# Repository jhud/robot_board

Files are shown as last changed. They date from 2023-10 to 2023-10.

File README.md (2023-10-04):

# Robot controller board

Controller board for building servo-based robots, such as hexapods.

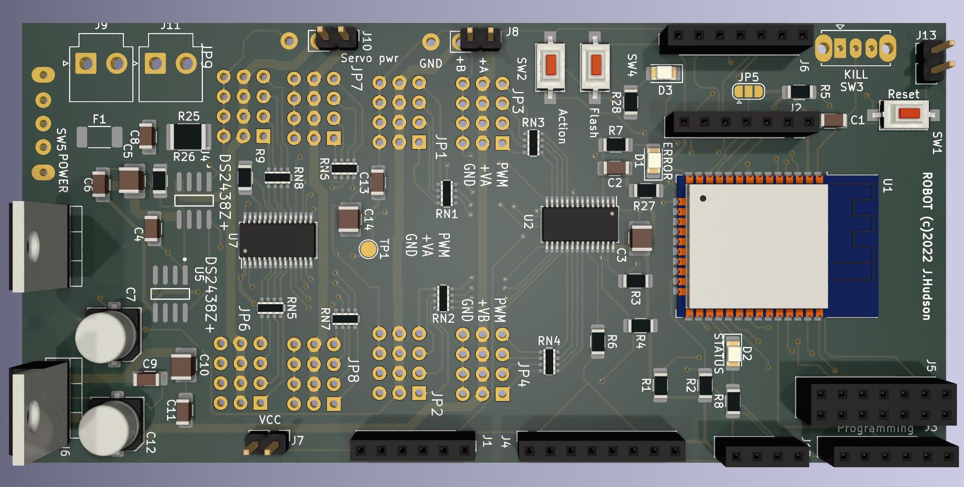
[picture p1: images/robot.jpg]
robot image

Render of board rev 2

This project was designed to allow rapid prototyping of different types of servos and sensors for walking robots: it's easy to switch out different sensors, and I2C buses are exposed for adding standard plugin components, such as those from Adafruit. But the board could be used for any projects needing a lot of servos.

The main benefit of this over a standard Arduino is the number of PWM pins and the server sockets, plus the power supply monitoring circuitry.

You should be able to get a standard "spiderbot" Arduino sketch running on this hardware quite easily: I'll shortly publish some test sketches and controller firmware.

Have fun!

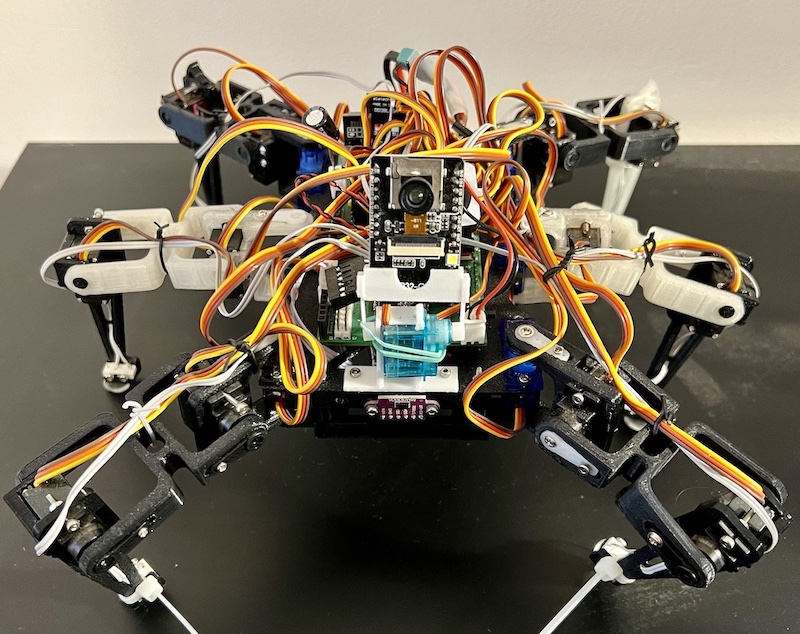
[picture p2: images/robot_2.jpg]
robot board

Board in action

## Features

Core features:
- ESP32 processor, Arduino compatible
- 32 PWM servo channels (ie max 10 legs)
- 6 foot contact sensors
- 7.6v LiPo battery, or power supply input
- Power supply monitoring for:
   - main battery voltage + current
   - 3.3v regulated rail voltage
   - 2x 5v rail servo voltages

With standard plugin modules installed in sockets:
- speech and audio output
- infrared beacon detection
- inertial measurement unit
- extra PWM channels

See it running here (video):

Hanging out with my robot and asking it to do things
[http://www.youtube.com/watch?v=hFirgdrsIpw](https://www.youtube.com/watch?v=hFirgdrsIpw)

## Building it

### ESP32 CAM

The ESP32 CAM module can run on 3.3v or 5v. If you are getting freezes and dropped frames from the camera, try running it from the robot's 5v rail instead of 3.3v.

The ESP32 CAM has a XC6206-2.8V regulator after its 3.3v regulator, and this component has a dropout voltage up to ~500mV according to the specs. My hypothesis is that the camera crashes on slight undervoltages.

So the 3.3v rail must be rock solid - this may not be the case with your regulator, so it's generally recommended to run the ESP32 CAM off the 5v rail. Even with many noisy servos, the camera works fine on the robot on the 5v rail.

### Pullup resistors

Pullups can vary between 2K and 10K - if there are problems communicating with I2C, try reducing the pullups. Higher pull-ups waste less power.

## Revisions

Note that the main branch is a work in progress: please take an earlier revision if you want a working layout. These are tested and working (with some minor noise issues and a couple of bodge wires needed).

- main branch is a work in progress: I am upgrading to ESP32-S3 and have fixed some noise issues and minor annoyances. Use an older tag if you want something that works.
- 2nd revision: 32 PWM channels onboard, 6 foot switches + power pins for IR proximity sensors
- 1st revision: 16 PWM channels, 4 foot switches

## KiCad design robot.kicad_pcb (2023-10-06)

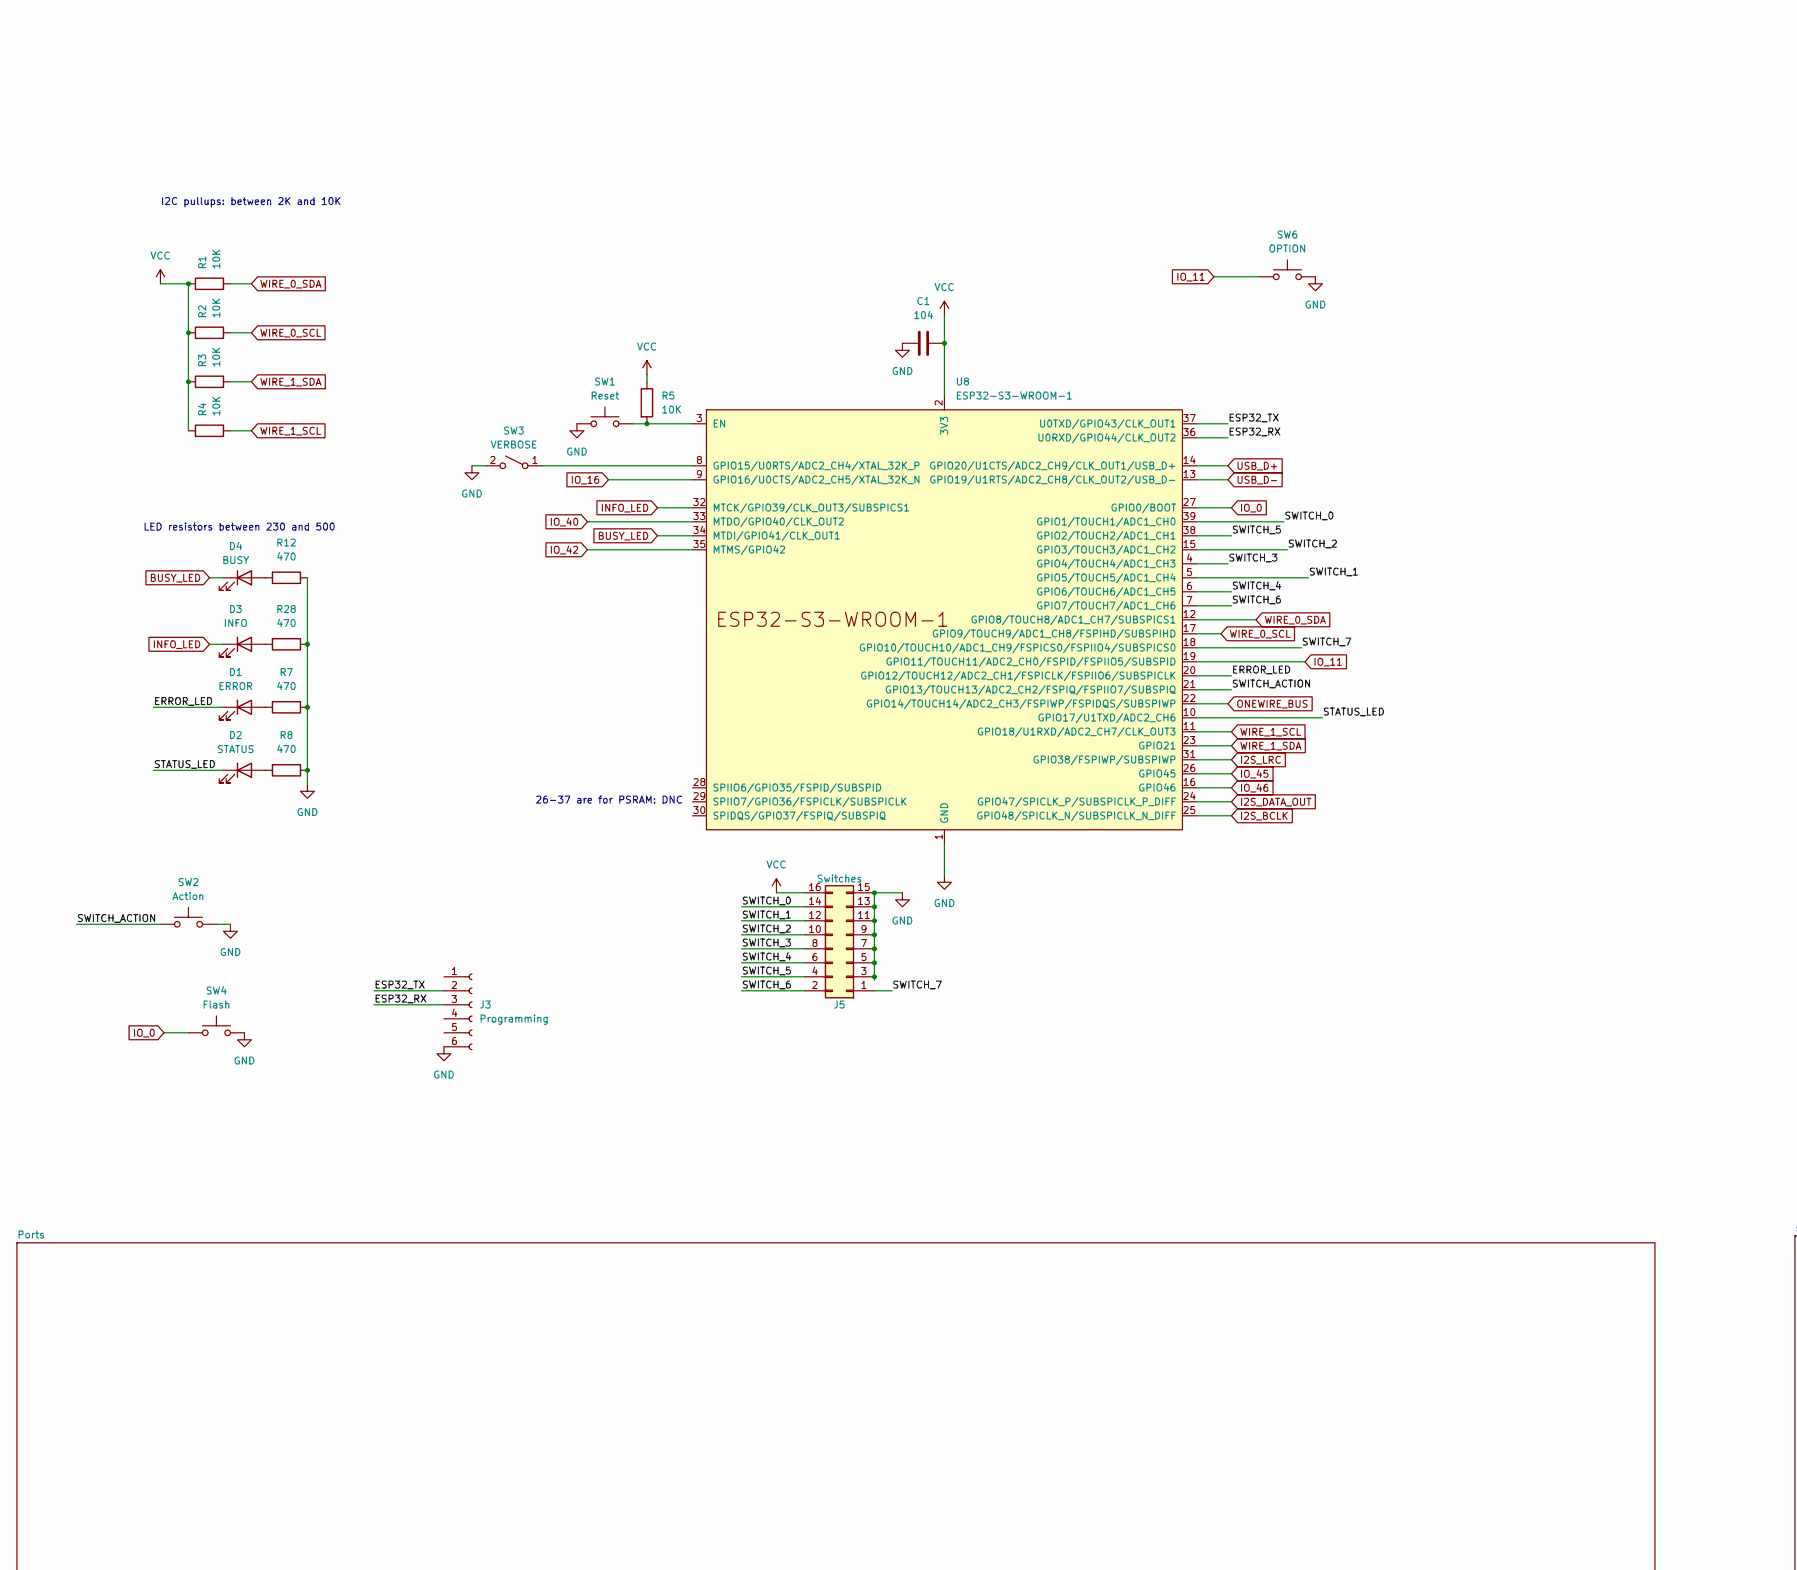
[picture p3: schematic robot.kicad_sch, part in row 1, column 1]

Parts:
C1: 104; C_1206_3216Metric_Pad1.33x1.80mm_HandSolder
D1: ERROR; LED_1206_3216Metric_Pad1.42x1.75mm_HandSolder
D2: STATUS; LED_1206_3216Metric_Pad1.42x1.75mm_HandSolder
D3: INFO; LED_1206_3216Metric_Pad1.42x1.75mm_HandSolder
D4: BUSY; LED_1206_3216Metric_Pad1.42x1.75mm_HandSolder
J3: Programming; PinSocket_1x06_P2.54mm_Vertical
J5: Switches; PinSocket_2x08_P2.54mm_Vertical
R1, R2, R3, R4, R5: 10K; R_1206_3216Metric_Pad1.30x1.75mm_HandSolder
R7, R8, R12, R28: 470; R_1206_3216Metric_Pad1.30x1.75mm_HandSolder
SW1: Reset; SW_SPST_CK_RS282G05A3
SW2: Action; SW_SPST_CK_RS282G05A3
SW3: VERBOSE; SW_Slide_1P2T_CK_OS102011MS2Q
SW4: Flash; SW_SPST_CK_RS282G05A3
SW6: OPTION; SW_SPST_CK_RS282G05A3
U8: ESP32-S3-WROOM-1; ESP32-S3-WROOM-1U

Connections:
/ERROR_LED: D1.1 (K), U8.20 (GPIO12/TOUCH12/ADC2_CH1/FSPICLK/FSPIIO6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)
/ESP32_RX: J3.3, U8.36 (U0RXD/GPIO44/CLK_OUT2)
/ESP32_TX: J3.2, U8.37 (U0TXD/GPIO43/CLK_OUT1)
/STATUS_LED: D2.1 (K), U8.10 (GPIO17/U1TXD/ADC2_CH6)
/SWITCH_0: J5.14, U8.39 (GPIO1/TOUCH1/ADC1_CH0)
/SWITCH_1: J5.12, U8.5 (GPIO5/TOUCH5/ADC1_CH4)
/SWITCH_2: J5.10, U8.15 (GPIO3/TOUCH3/ADC1_CH2)
/SWITCH_3: J5.8, U8.4 (GPIO4/TOUCH4/ADC1_CH3)
/SWITCH_4: J5.6, U8.6 (GPIO6/TOUCH6/ADC1_CH5)
/SWITCH_5: J5.4, U8.38 (GPIO2/TOUCH2/ADC1_CH1)
/SWITCH_6: J5.2, U8.7 (GPIO7/TOUCH7/ADC1_CH6)
/SWITCH_7: J5.1, U8.18 (GPIO10/TOUCH10/ADC1_CH9/FSPICS0/FSPIIO4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)
/SWITCH_ACTION: SW2.1, U8.21 (GPIO13/TOUCH13/ADC2_CH2/FSPIQ/FSPIIO7/S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)
BUSY_LED: D4.1 (K), U8.34 (MTDI/GPIO41/CLK_OUT1)
GND: C1.1, J3.6, J5.3, J5.5, J5.7, J5.9, J5.11, J5.13, J5.15, R7.1, R8.1, R12.1, R28.1, SW1.1, SW2.2, SW3.2 (B), SW4.2, SW6.2, U8.1 (GND), U8.40 (GND), U8.41 (GND); also elsewhere on the board
I2S_BCLK: U8.25 (GPIO48/SPICLK_N/SUBSPICLK_N_DIFF); also elsewhere on the board
I2S_DATA_OUT: U8.24 (GPIO47/SPICLK_P/SUBSPICLK_P_DIFF); also elsewhere on the board
I2S_LRC: U8.31 (GPIO38/FSPIWP/SUBSPIWP); also elsewhere on the board
INFO_LED: D3.1 (K), U8.32 (MTCK/GPIO39/CLK_OUT3/SUBSPICS1)
IO_0: SW4.1, U8.27 (GPIO0/BOOT)
IO_11: SW6.1, U8.19 (GPIO11/TOUCH11/ADC2_CH0/FSPID/FSPIIO5/S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)
IO_16: U8.9 (GPIO16/U0CTS/ADC2_CH5/XTAL_32K_N); also elsewhere on the board
IO_40: U8.33 (MTDO/GPIO40/CLK_OUT2); also elsewhere on the board
IO_42: U8.35 (MTMS/GPIO42); also elsewhere on the board
IO_45: U8.26 (GPIO45); also elsewhere on the board
IO_46: U8.16 (GPIO46); also elsewhere on the board
unnamed: D1.2 (A), R7.2
unnamed: D2.2 (A), R8.2
unnamed: D3.2 (A), R28.2
unnamed: D4.2 (A), R12.2
unnamed: SW3.1 (A), U8.8 (GPIO15/U0RTS/ADC2_CH4/XTAL_32K_P)
unnamed: R5.2, SW1.2, U8.3 (EN)
ONEWIRE_BUS: U8.22 (GPIO14/TOUCH14/ADC2_CH3/FSPIWP/FSPIDQS/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); also elsewhere on the board
USB_D+: U8.14 (GPIO20/U1CTS/ADC2_CH9/CLK_OUT1/USB_D+); also elsewhere on the board
USB_D-: U8.13 (GPIO19/U1RTS/ADC2_CH8/CLK_OUT2/USB_D-); also elsewhere on the board
VCC: C1.2, J5.16, R1.1, R2.1, R3.1, R4.1, R5.1, U8.2 (3V3); also elsewhere on the board
WIRE_0_SCL: R2.2, U8.17 (GPIO9/TOUCH9/ADC1_CH8/FSPIHD/SUBSPIHD); also elsewhere on the board
WIRE_0_SDA: R1.2, U8.12 (GPIO8/TOUCH8/ADC1_CH7/SUBSPICS1); also elsewhere on the board

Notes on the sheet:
26-37 are for PSRAM: DNC
LED resistors between 230 and 500
I2C pullups: between 2K and 10K

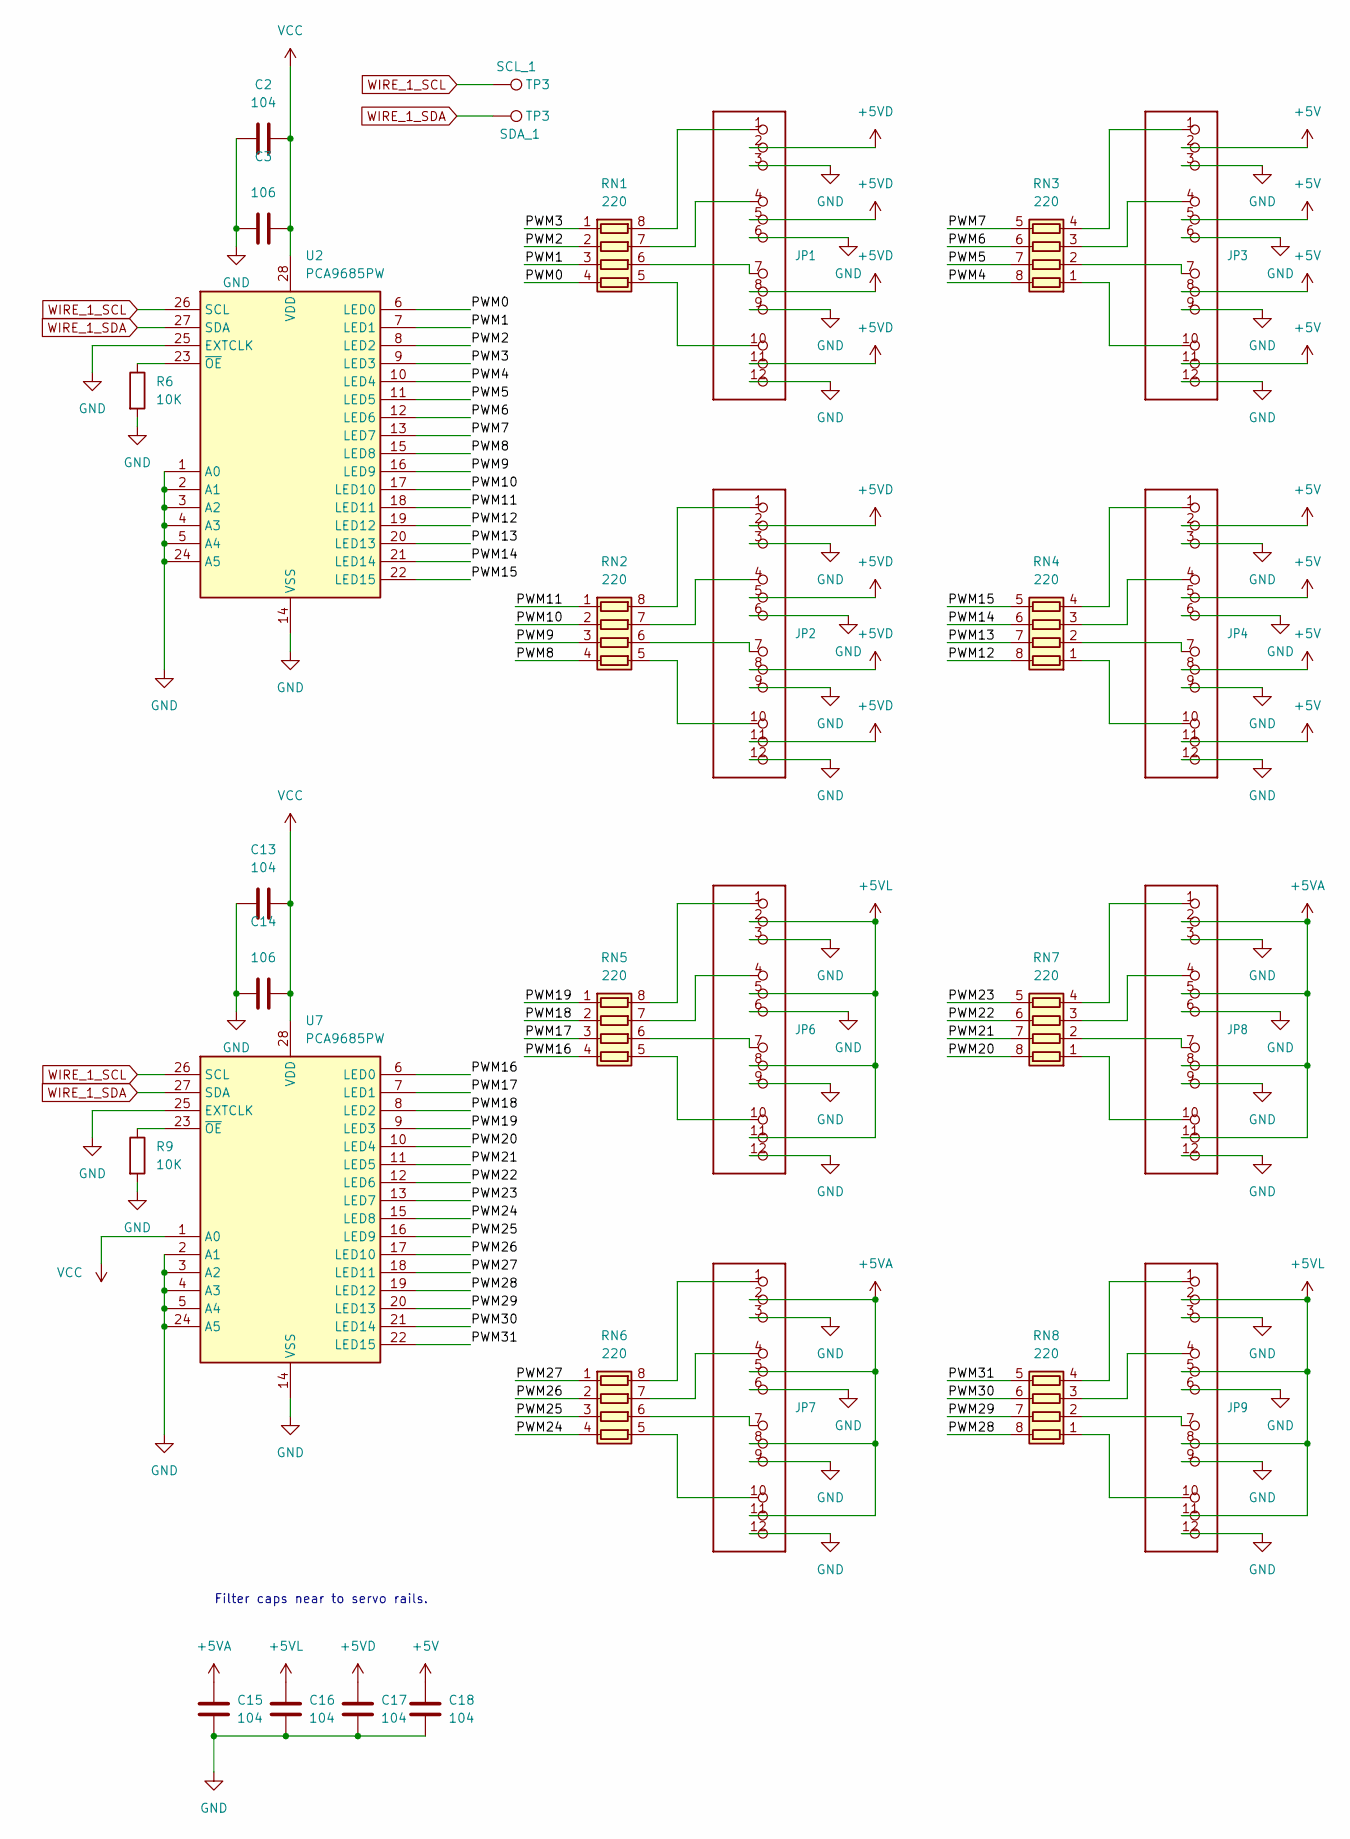
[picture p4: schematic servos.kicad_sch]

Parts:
C2, C13, C15, C16, C17, C18: 104; C_1206_3216Metric_Pad1.33x1.80mm_HandSolder
C3, C14: 106; C_1210_3225Metric_Pad1.33x2.70mm_HandSolder
JP1, JP2, JP3, JP4, JP6, JP7, JP8, JP9: HEADER-3X04; 3X04
R6, R9: 10K; R_1206_3216Metric_Pad1.30x1.75mm_HandSolder
RN1, RN2, RN3, RN4, RN5, RN6, RN7, RN8: 220; R_Array_Concave_4x0603
TP3: SCL_1; TestPoint_Pad_D2.0mm
U2, U7: PCA9685PW; TSSOP-28_4.4x9.7mm_P0.65mm

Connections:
+5V: C18.1, JP3.2, JP3.5, JP3.8, JP3.11, JP4.2, JP4.5, JP4.8, JP4.11; also elsewhere on the board
+5VD: C17.1, JP1.2, JP1.5, JP1.8, JP1.11, JP2.2, JP2.5, JP2.8, JP2.11; also elsewhere on the board
+5VL: C16.1, JP6.2, JP6.5, JP6.8, JP6.11, JP9.2, JP9.5, JP9.8, JP9.11; also elsewhere on the board
/servos/PWM0: RN1.4 (R4.1), U2.6 (LED0)
/servos/PWM1: RN1.3 (R3.1), U2.7 (LED1)
/servos/PWM2: RN1.2 (R2.1), U2.8 (LED2)
/servos/PWM3: RN1.1 (R1.1), U2.9 (LED3)
/servos/PWM4: RN3.8 (R1.2), U2.10 (LED4)
/servos/PWM5: RN3.7 (R2.2), U2.11 (LED5)
/servos/PWM6: RN3.6 (R3.2), U2.12 (LED6)
/servos/PWM7: RN3.5 (R4.2), U2.13 (LED7)
/servos/PWM8: RN2.4 (R4.1), U2.15 (LED8)
/servos/PWM9: RN2.3 (R3.1), U2.16 (LED9)
/servos/PWM10: RN2.2 (R2.1), U2.17 (LED10)
/servos/PWM11: RN2.1 (R1.1), U2.18 (LED11)
/servos/PWM12: RN4.8 (R1.2), U2.19 (LED12)
/servos/PWM13: RN4.7 (R2.2), U2.20 (LED13)
/servos/PWM14: RN4.6 (R3.2), U2.21 (LED14)
/servos/PWM15: RN4.5 (R4.2), U2.22 (LED15)
/servos/PWM16: RN5.4 (R4.1), U7.6 (LED0)
/servos/PWM17: RN5.3 (R3.1), U7.7 (LED1)
/servos/PWM18: RN5.2 (R2.1), U7.8 (LED2)
/servos/PWM19: RN5.1 (R1.1), U7.9 (LED3)
/servos/PWM20: RN7.8 (R1.2), U7.10 (LED4)
/servos/PWM21: RN7.7 (R2.2), U7.11 (LED5)
/servos/PWM22: RN7.6 (R3.2), U7.12 (LED6)
/servos/PWM23: RN7.5 (R4.2), U7.13 (LED7)
/servos/PWM24: RN6.4 (R4.1), U7.15 (LED8)
/servos/PWM25: RN6.3 (R3.1), U7.16 (LED9)
/servos/PWM26: RN6.2 (R2.1), U7.17 (LED10)
/servos/PWM27: RN6.1 (R1.1), U7.18 (LED11)
/servos/PWM28: RN8.8 (R1.2), U7.19 (LED12)
/servos/PWM29: RN8.7 (R2.2), U7.20 (LED13)
/servos/PWM30: RN8.6 (R3.2), U7.21 (LED14)
/servos/PWM31: RN8.5 (R4.2), U7.22 (LED15)
GND: C2.2, C3.1, C13.2, C14.1, C15.2, C16.2, C17.2, C18.2, JP1.3, JP1.6, JP1.9, JP1.12, JP2.3, JP2.6, JP2.9, JP2.12, JP3.3, JP3.6, JP3.9, JP3.12, JP4.3, JP4.6, JP4.9, JP4.12, JP6.3, JP6.6, JP6.9, JP6.12, JP7.3, JP7.6, JP7.9, JP7.12, JP8.3, JP8.6, JP8.9, JP8.12, JP9.3, JP9.6, JP9.9, JP9.12, R6.2, R9.2, U2.1 (A0), U2.2 (A1), U2.3 (A2), U2.4 (A3), U2.5 (A4), U2.14 (VSS), U2.24 (A5), U2.25 (EXTCLK), U7.2 (A1), U7.3 (A2), U7.4 (A3), U7.5 (A4), U7.14 (VSS), U7.24 (A5), U7.25 (EXTCLK); also elsewhere on the board
unnamed: JP1.1, RN1.8 (R1.2)
unnamed: JP1.4, RN1.7 (R2.2)
unnamed: JP1.7, RN1.6 (R3.2)
unnamed: JP1.10, RN1.5 (R4.2)
unnamed: JP2.1, RN2.8 (R1.2)
unnamed: JP2.4, RN2.7 (R2.2)
unnamed: JP2.7, RN2.6 (R3.2)
unnamed: JP2.10, RN2.5 (R4.2)
unnamed: JP3.10, RN3.1 (R1.1)
unnamed: JP3.7, RN3.2 (R2.1)
unnamed: JP3.4, RN3.3 (R3.1)
unnamed: JP3.1, RN3.4 (R4.1)
unnamed: JP4.10, RN4.1 (R1.1)
unnamed: JP4.7, RN4.2 (R2.1)
unnamed: JP4.4, RN4.3 (R3.1)
unnamed: JP4.1, RN4.4 (R4.1)
unnamed: JP6.1, RN5.8 (R1.2)
unnamed: JP6.4, RN5.7 (R2.2)
unnamed: JP6.7, RN5.6 (R3.2)
unnamed: JP6.10, RN5.5 (R4.2)
unnamed: JP7.1, RN6.8 (R1.2)
unnamed: JP7.4, RN6.7 (R2.2)
unnamed: JP7.7, RN6.6 (R3.2)
unnamed: JP7.10, RN6.5 (R4.2)
unnamed: JP8.10, RN7.1 (R1.1)
unnamed: JP8.7, RN7.2 (R2.1)
unnamed: JP8.4, RN7.3 (R3.1)
unnamed: JP8.1, RN7.4 (R4.1)
unnamed: JP9.10, RN8.1 (R1.1)
unnamed: JP9.7, RN8.2 (R2.1)
unnamed: JP9.4, RN8.3 (R3.1)
unnamed: JP9.1, RN8.4 (R4.1)
unnamed: R6.1, U2.23 (~OE)
unnamed: R9.1, U7.23 (~OE)
VCC: C2.1, C3.2, C13.1, C14.2, U2.28 (VDD), U7.1 (A0), U7.28 (VDD); also elsewhere on the board

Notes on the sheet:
Filter caps near to servo rails.

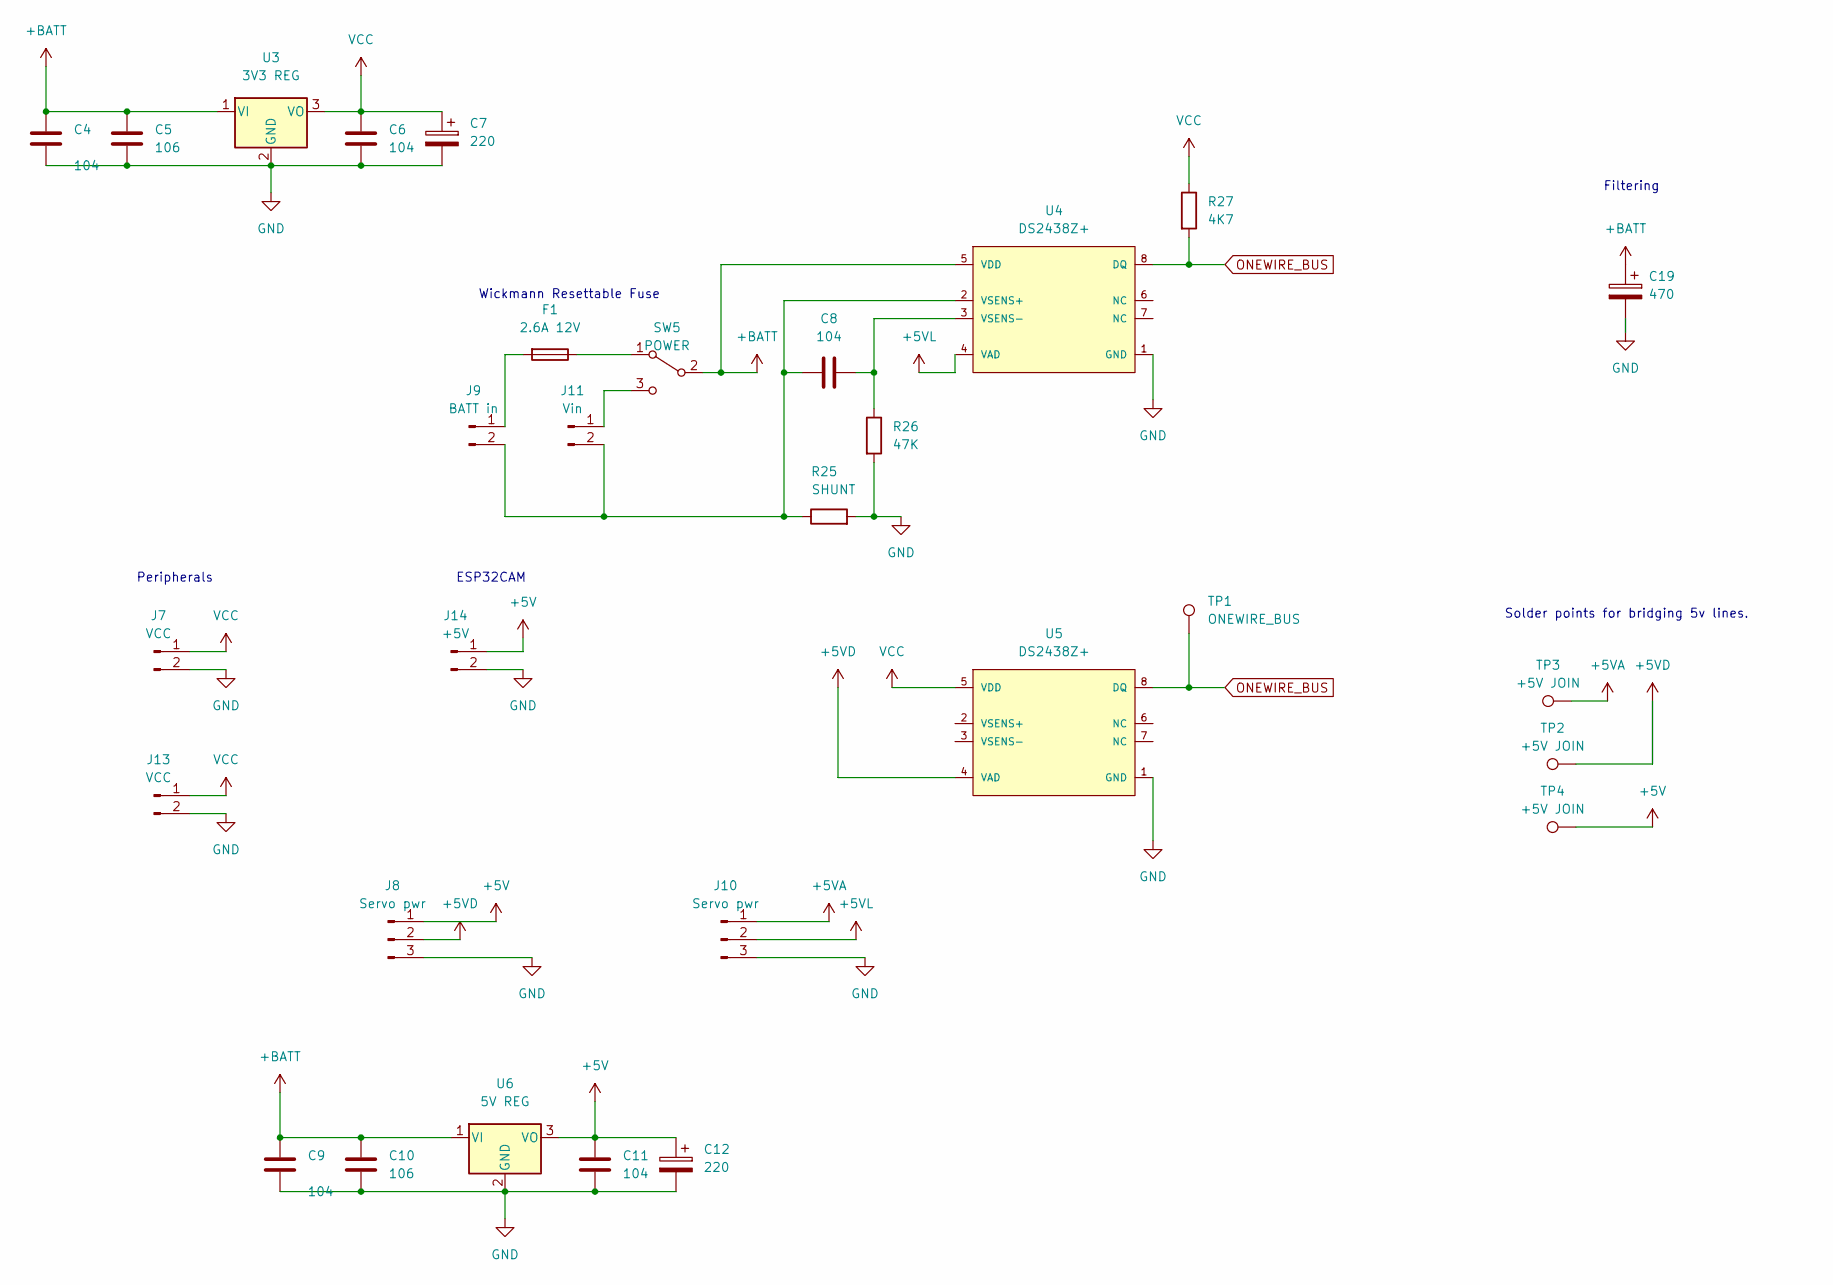
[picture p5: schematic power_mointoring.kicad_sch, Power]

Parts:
C4, C6, C8, C9, C11: 104; C_1206_3216Metric_Pad1.33x1.80mm_HandSolder
C5, C10: 106; C_1210_3225Metric_Pad1.33x2.70mm_HandSolder
C7, C12: 220; C_Elec_6.3x5.4
C19: 470; C_Elec_6.3x7.7
F1: 2.6A 12V; Fuse_2010_5025Metric
J7, J13: VCC; PinHeader_1x02_P2.54mm_Vertical
J8, J10: Servo pwr; Connector_SolderPadsx3
J9: BATT in; JST_VH_B2P-VH-B_1x02_P3.96mm_Vertical
J11: Vin; JST_VH_B2P-VH-B_1x02_P3.96mm_Vertical
J14: +5V; PinHeader_1x02_P2.54mm_Vertical
R25: SHUNT; R_1812_4532Metric_Pad1.30x3.40mm_HandSolder
R26: 47K; R_1206_3216Metric_Pad1.30x1.75mm_HandSolder
R27: 4K7; R_1206_3216Metric_Pad1.30x1.75mm_HandSolder
SW5: POWER; Switch-SS12F23
TP1: ONEWIRE_BUS; TestPoint_Pad_D2.0mm
TP2, TP3, TP4: +5V JOIN; TestPoint_Pad_D2.0mm
U3: 3V3 REG; TO-220-3_Vertical
U4, U5: DS2438Z+; Maxim-S8-5-0-P-IPC_A; mouser part number 700-DS2438Z; digikey description IC MONITOR SMART BATTERY 8-SOIC
U6: 5V REG; TO-220-3_Vertical

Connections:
+5V: C11.1, C12.1, J8.1, J14.1, TP4.1, U6.3 (VO); also elsewhere on the board
+5VD: J8.2, TP2.1, U5.4 (VAD); also elsewhere on the board
+5VL: J10.2, U4.4 (VAD); also elsewhere on the board
+BATT: C4.1, C5.1, C9.1, C10.1, C19.1, SW5.2 (B), U3.1 (VI), U4.5 (VDD), U6.1 (VI)
GND: C4.2, C5.2, C6.2, C7.2, C9.2, C10.2, C11.2, C12.2, C19.2, J7.2, J8.3, J10.3, J13.2, J14.2, R25.2, R26.2, U3.2 (GND), U4.1 (GND), U5.1 (GND), U6.2 (GND); also elsewhere on the board
unnamed: F1.2, J9.1
unnamed: J11.1, SW5.3 (C)
unnamed: C8.2, J9.2, J11.2, R25.1, U4.2 (VSENS+)
unnamed: F1.1, SW5.1 (A)
unnamed: C8.1, R26.1, U4.3 (VSENS-)
ONEWIRE_BUS: R27.2, TP1.1, U4.8 (DQ), U5.8 (DQ); also elsewhere on the board
VCC: C6.1, C7.1, J7.1, J13.1, R27.1, U3.3 (VO), U5.5 (VDD); also elsewhere on the board

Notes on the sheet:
Filtering
ESP32CAM
Solder points for bridging 5v lines.
Wickmann Resettable Fuse
Peripherals

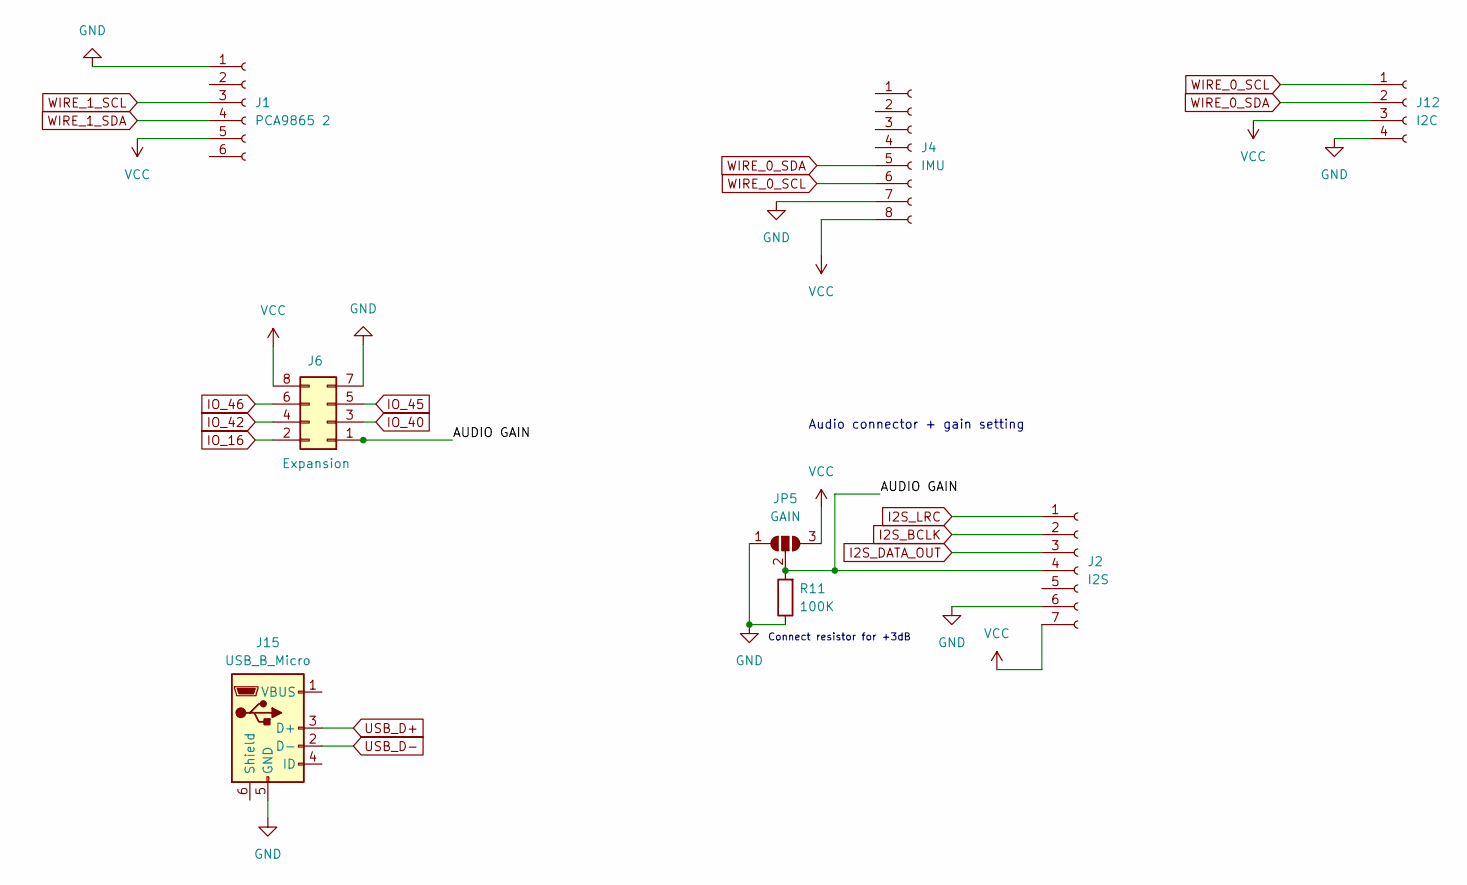
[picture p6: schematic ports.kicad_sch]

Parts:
J1: PCA9865 2; PinSocket_1x06_P2.54mm_Vertical
J2: I2S; PinSocket_1x07_P2.54mm_Vertical
J4: IMU; PinSocket_1x08_P2.54mm_Vertical
J6: Expansion; PinSocket_2x04_P2.54mm_Vertical
J12: I2C; PinSocket_1x04_P2.54mm_Vertical
J15: USB_B_Micro; USB_Micro-B_Amphenol_10104110_Horizontal
JP5: GAIN; SolderJumper-3_P1.3mm_Open_RoundedPad1.0x1.5mm
R11: 100K; R_1206_3216Metric_Pad1.30x1.75mm_HandSolder

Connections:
/Ports/AUDIO GAIN: J2.4, J6.1, JP5.2 (C), R11.2
GND: J1.1, J2.6, J4.7, J6.7, J12.4, J15.5 (GND), JP5.1 (A), R11.1; also elsewhere on the board
I2S_BCLK: J2.2; also elsewhere on the board
I2S_DATA_OUT: J2.3; also elsewhere on the board
I2S_LRC: J2.1; also elsewhere on the board
IO_16: J6.2; also elsewhere on the board
IO_40: J6.3; also elsewhere on the board
IO_42: J6.4; also elsewhere on the board
IO_45: J6.5; also elsewhere on the board
IO_46: J6.6; also elsewhere on the board
USB_D+: J15.3 (D+); also elsewhere on the board
USB_D-: J15.2 (D-); also elsewhere on the board
VCC: J1.5, J2.7, J4.8, J6.8, J12.3, JP5.3 (B); also elsewhere on the board
WIRE_0_SCL: J4.6, J12.1; also elsewhere on the board
WIRE_0_SDA: J4.5, J12.2; also elsewhere on the board

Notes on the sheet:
Connect resistor for +3dB
Audio connector + gain setting

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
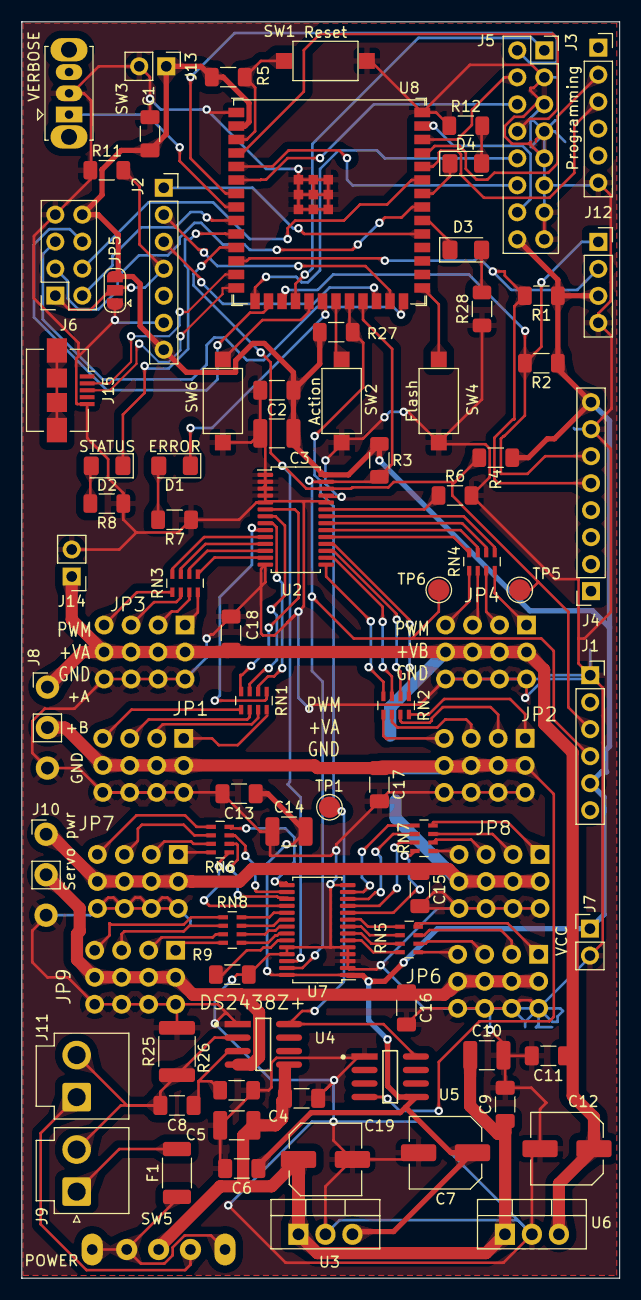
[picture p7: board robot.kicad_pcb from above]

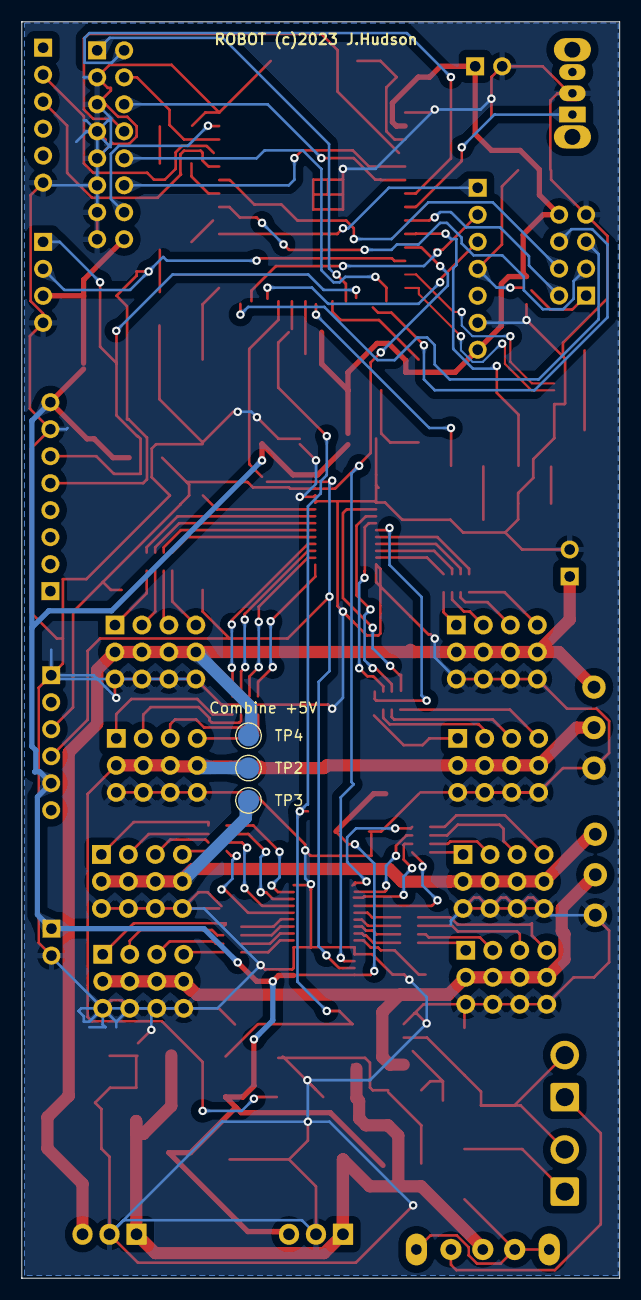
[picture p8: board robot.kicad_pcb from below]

Board: 2 copper layers, 56.3 x 118.2 mm, 90 parts (3 on the bottom side), 117 nets.

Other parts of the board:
TP5: SCL_1; TestPoint_Pad_D2.0mm
TP6: SDA_1; TestPoint_Pad_D2.0mm

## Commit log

2022-12-30 Layed out board, not routed
    [power_mointoring.kicad_sch, robot.kicad_pcb, robot.kicad_sch]
2022-12-30 Added extra mounting hole
    [robot.kicad_pcb]
2022-12-30 Ready to route.
    [robot.kicad_pcb]
2022-12-31 Ready for fab.
    [power_mointoring.kicad_sch, robot.kicad_pcb, robot.kicad_sch]
2023-01-15 Added minor footprint changes after trying to build the board. Added pin to switch battery to Vin.
    [power_mointoring.kicad_sch, robot.kicad_pcb, robot.kicad_sch]
2023-02-22 Added extra pins and input from revision 1.
    [power_mointoring.kicad_sch, robot.kicad_pcb, robot.kicad_sch]
2023-02-28 Added revision 2 features, not routed.
    [ports.kicad_sch, power_mointoring.kicad_sch, robot.kicad_sch]
2023-02-28 Board ready to go.
    [power_mointoring.kicad_sch, robot.kicad_pcb, robot.kicad_sch]
2023-02-28 Clean chematic
    [power_mointoring.kicad_sch, robot.kicad_pcb, robot.kicad_sch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]
2023-03-02 Cleaned revision 2.
    [ports.kicad_sch, robot.kicad_pcb]
2023-05-09 Very minor tweaks for board version 3.
    [ports.kicad_sch, power_mointoring.kicad_sch, robot.kicad_pcb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]
2023-06-13 Upgrade to version 7, started adding new WROOM-S3
    [ports.kicad_sch, power_mointoring.kicad_sch, robot.kicad_pcb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]
2023-06-15 started wiring up s3
    [robot.kicad_pcb, robot.kicad_sch]
2023-10-02 Added larger filter caps + across the battery
    [power_mointoring.kicad_sch, robot.kicad_pcb, robot.kicad_sch]
2023-10-04 Added info about ESP32 CAM.
2023-10-04 Removed old ESP32, added ESP32 S3.
    [ports.kicad_sch, power_mointoring.kicad_sch, robot.kicad_pcb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]
2023-10-05 Finished routing board revision 3: ready for first PCB run.
    [ports.kicad_sch, robot.kicad_pcb, servos.kicad_sch]
2023-10-06 Sent off for fabrication, added test points.
    [robot.kicad_pcb]
2023-10-29 Switched out GPIO3 for GPIO16 because it is a strapping pin with no pullup.
    [ports.kicad_sch, robot.kicad_sch]
2023-10-30 Added missing power bridge point for 1 rail.
    [power_mointoring.kicad_sch]
2023-11-14 Switched a few pins which were glitchy in on the hardware to known good pins. May have just been a faulty ESP32, but just to be sure.
    [robot.kicad_sch]
2023-11-18 Flipped current sense resistor connections - it was the wrong way around.
    [power_mointoring.kicad_sch]

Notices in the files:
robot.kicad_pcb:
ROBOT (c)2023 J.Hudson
